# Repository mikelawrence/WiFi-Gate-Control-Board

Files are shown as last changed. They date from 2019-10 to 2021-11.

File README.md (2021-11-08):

# WiFi Gate Controller Board

This board performs the same functions as my [WiFi Gate Controller](https://github.com/mikelawrence/WiFi-Gate-Controller), which was designed to add WiFi and Home Assistant control to an existing US Automation Gate Opener board, while providing motor control and standard gate inputs. This board will replace a US Automation Gate Opener board. All inputs are now generalized and also support 10k resistor monitoring for safety devices like edge or photoelectric inputs.

This PCB design uses my custom libraries available here [Mike's KiCad Libraries](https://github.com/mikelawrence/KiCad-Libraries).

This PCB was designed with [KiCad 5.1.4](http://kicad.org).

_Note: Multiple ICs and Modules have exposed pads on the bottom which requires either a reflow oven or hot air to solder properly._

For Bill of Materials generation I use my version of [KiBoM](https://github.com/mikelawrence/KiBoM) forked from [SchrodingersGat](https://github.com/SchrodingersGat/KiBoM).

## Status

* Rev 1.1 PCB was built by and received from PCBWay.
  * This is a 4 layer PCB using 2 oz. copper for all layers and is relatively expensive.
  * Board has been assembled with no problems.
  * Motor interface still needs to be tested everything else is good.
  * You can order PCB from [PCBWay](https://www.pcbway.com/project/shareproject/WiFi_Gate_Control_Board_Rev_1_1.html).
  * You can order parts from Mouser using this [shared BOM](https://www.mouser.com/ProjectManager/ProjectDetail.aspx?AccessID=5c81251866).

* Rev 1.0 PCB was built by and received from PCBWay. Testing is complete.
  * PCBWay built the board.
  * I2C interface to TCA6424A, TCA6408A and LPC5024 verified. Reset not connected error found and corrected in Rev 1.1.
  * 12VDC input and reverse polarity protection verified.
  * LED circuitry and power supply verified.
  * All 12 Inputs verified. This includes switch closure and 10k monitoring.
  * All +12V switched outputs verified. Overload tested also.
  * All 2 Normally Open outputs tested.
  * Full-bridge motor control has been tested up to 30A. Far more than needed.
  * Motor current sensing verified. Removed U26 and connected IN input for each half-bridge directly to processor. Needed to set both half-bridges to active low so MIS offset could be measured unloaded.

## Board Preview

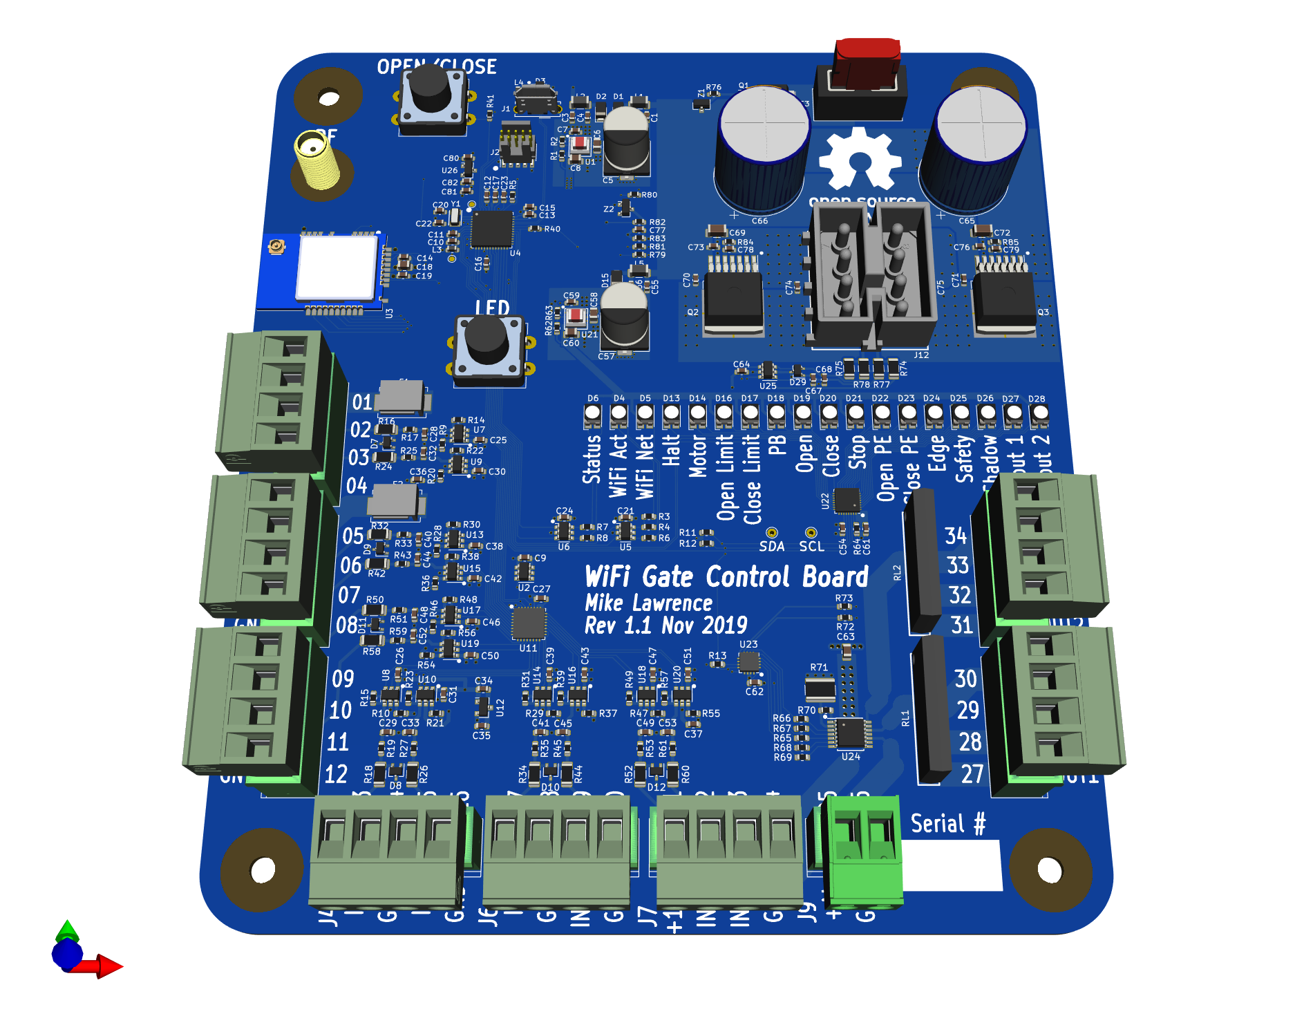
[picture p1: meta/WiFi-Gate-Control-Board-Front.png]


## Design

Intended to replace a US Automatic Patriot Board, this board can directly drive a single gate actuator in both directions. Multiple generic inputs are provided on board to make connection to existing standard gate functionality (open, close, pushbutton...) easy. By providing a WiFi connection to a MQTT server this board can be controlled via standard home automation software (Home Assistant).

Board size is 5.50" X 6.25". This board is smaller than the standard size of a US Automatic Patriot Board but matches existing spacer locations.

### Input Power

The main input connector (J12) provides connections to both the battery and motor. This connector is used by both US Automatic and Apollo gate openers. See pinout below.

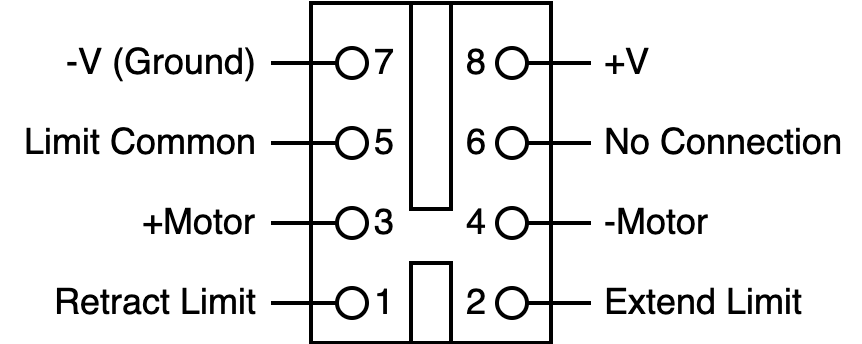
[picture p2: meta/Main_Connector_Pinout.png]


A 15 Amp fuse protects the entire board. DC input range is 12V nominal (5V - 17V). Idle input power consumption is pretty variable running from 69mW to 1.38W with an average around 179mW. Peak power is during WiFi transmit.

There are two identical power supplies. U1 powers most of the board via 3.3V. U1's power source is either main power (J12) or the USB connector (J1) so the microprocessor can be programmed on the bench without main power. All LEDs on the board are powered by a separate power supply (U21) which can be turned off by the microprocessor. This substantially reduces power consumption

### Board connections

There are nine screw terminal blocks with removable headers on the board used to connect with all gate functions.

| Terminal | Name  | Conn  | Description |
| :---: | :---: | :---: | :--- |
| 01 | +12V  | J3 | +12V power, Always on, fused 0.75A |
| 02 | IN1 | J3 | Input 1 (Radio) |
| 03 | IN2 | J3 | Input 2 |
| 04 | GND | J3 | Common Ground |
| 05 | +12V  | J5 | +12V power, Always on, fused 0.75A |
| 06 | IN3 | J5 | Input 3 |
| 07 | IN4 | J5 | Input 4 |
| 08 | GND | J5 | Common Ground |
| 09 | IN5 | J8 | Input 5 |
| 10 | GND | J8 | Common Ground |
| 11 | IN6 | J8 | Input 6 |
| 12 | GND | J8 | Common Ground |
| 13 | IN7 | J4 | Input 7 |
| 14 | GND | J4 | Common Ground |
| 15 | IN8 | J4 | Input 8 |
| 16 | GND | J4 | Common Ground |
| 17 | IN9 | J6 | Input 9 |
| 18 | GND | J6 | Common Ground |
| 19 | IN10  | J6 | Input 10 |
| 20 | GND | J6 | Common Ground |
| 21 | IN11  | J7 | +12V power, Switched PhotoEye power |
| 22 | GND | J7 | Input 11 |
| 23 | IN12  | J7 | Input 12 |
| 24 | GND | J7 | Common Ground |
| 25 | +AL | J9 | +12V power, Switched Alarm power |
| 26 | GND | J9 | Common Ground |
| 27 | OUT1  | J7 | Output 1, NO switch Output 1 |
| 28 | COM1  | J7 | Common 1, NO switch Output 1 |
| 29 | GND | J9 | Common Ground |
| 30 | +12V  | J9 | +12V power, Switched Output 1 power |
| 31 | OUT2  | J7 | Output 2, NO switch Output 2 |
| 32 | COM2  | J7 | Common 2, NO switch Output 2 |
| 33 | GND | J9 | Common Ground |
| 34 | +12V  | J9 | +12V power, Switched Output 2 power |

### Inputs

There are 12 identical physical inputs on this board. Each input can support Normally Open, Normally Closed, and 10k Monitored Normally Open inputs. A Normally Open input is a dry contact that is open when inactive and closed (shorted) when active. A Normally Closed input is the opposite; closed (shorted) when inactive and open when active. A 10k Monitored input is a Normally Open dry contact with a 8k to 10k resistor across the contacts and is normally used for safety inputs. The resistor allows the connections to the contact to be monitored while inactive. The most current efficient input is the Normally Open input which requires no additional current when inactive. The 10k Monitored input requires an additional 49μA and the Normally Closed input requires a 59μA per input while inactive.

Each input is actually a pair of connections: input and ground (negative terminal of battery). This means the ground side is the same (connected) on all inputs and external wiring must take this into account. Each input can be configured for different gate input types in software as shown in the table below.

| Input | Other Names | Type | Monitored | Action |
| :--- | :--- | :---: | :---: | :--- |
| Push Button | | NO | No | Cycle through Open/Stop/Close commands to gate. |
| Close | | NO | No | While active, close gate and holds it closed. |
| Open | Exit, Free Exit | NO | No | While active, opens gate and holds it open. |
| Stop | | NC | No | While active, stops the gate and holds it in position. |
| Open PhotoEye  | | NO or NC | Yes | While active, stops an opening gate or prevents gate from opening. |
| Close PhotoEye | | NO or NC | Yes | While active, reverses a closing gate to full open and holds it open. |
| Safety Edge | | NO | Yes | When activated, stops and momentarily reverses a moving gate. |
| Safety Loop | Reverse Loop | NO | Yes | While active, reverses a closing gate to full open and holds it open. |
| Shadow Loop | Center Loop, Under Gate Loop | NO | Yes | While active, prevents a closed gate from opening, prevents an open gate from closing, or reverses a closing gate to fully open and holds it open. |
| Input 1 | | NO or NC | Yes | Has no gate function. Can be used to monitor say a mailbox door.
| Input 2 | | NO or NC | Yes | Has no gate function.

Look at [Safety Edge Circuit calculations](drawings/Safety Edge Circuit calculations.pdf) for an explanation of how the input circuits with 10k monitoring work.

### Outputs

There are 4 switched power outputs on the board. J7 is used for PhotoEye connections and thus the +12V is switched on only during gate motion. The Alarm +AL is switched to +12V when alarm is active. The +12V on J10 and J11 output connectors are switched based on output settings.

There are several to be defined output settings here.

### SAMD ARM Processor and WiFi Module

The ARM processor and ATWINC1500 WiFi module are wired identical to the MKR1000 Arduino board, thus the Arduino development environment is used for software development and the ATWINC1500 module is directly supported.

## Setup

### Arduino Setup

This board is designed to mimic a [MKR1000](https://store.arduino.cc/usa/arduino-mkr1000) board from Arduino. Make sure the the MKR1000 board is supported by installing. Do this by opening the Board Manager as shown below.

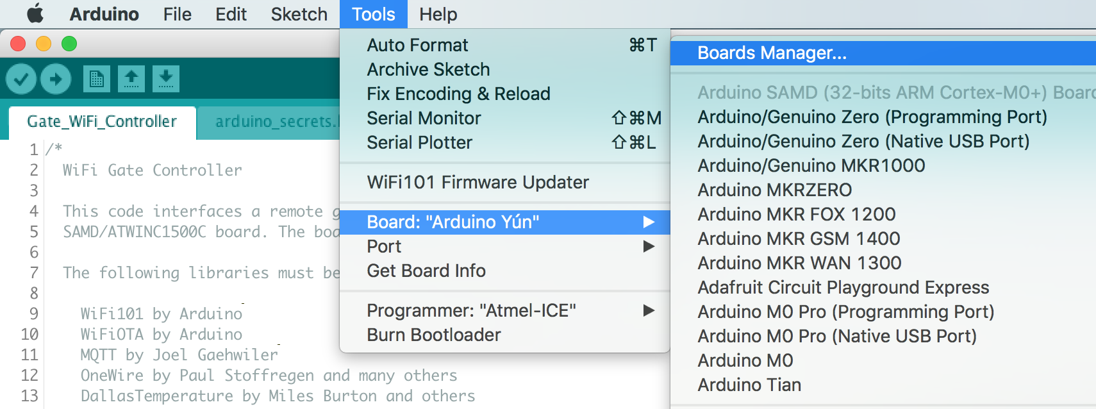
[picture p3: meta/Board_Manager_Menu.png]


Type in "samd" in the filter edit and you will see several options. Select "Arduino SAMD Boards (32-bits ARM Cortex-M0+)" and install the latest version as shown below.

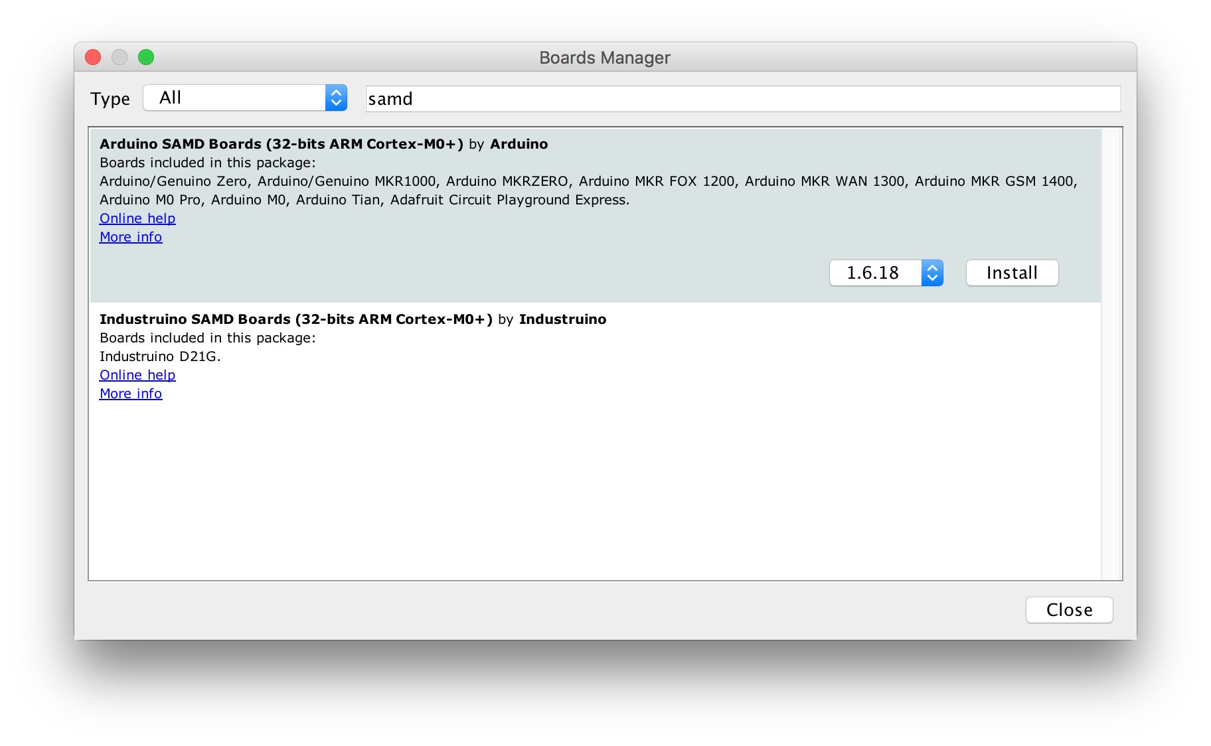
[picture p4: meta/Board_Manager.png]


It will take a few minutes to download and install the board package. Once complete it's time to install the necessary libraries. Start by opening the Library Manager as shown below.

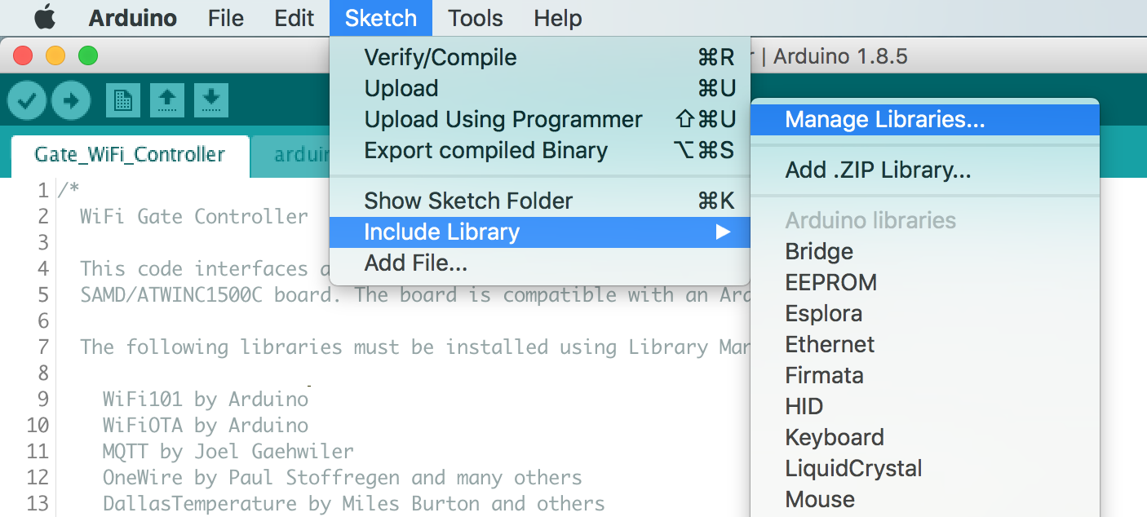
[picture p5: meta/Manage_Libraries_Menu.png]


Type in "mqtt" in the filter edit and scroll down until you see "MQTT by Joel Gaehwiler" as shown below.

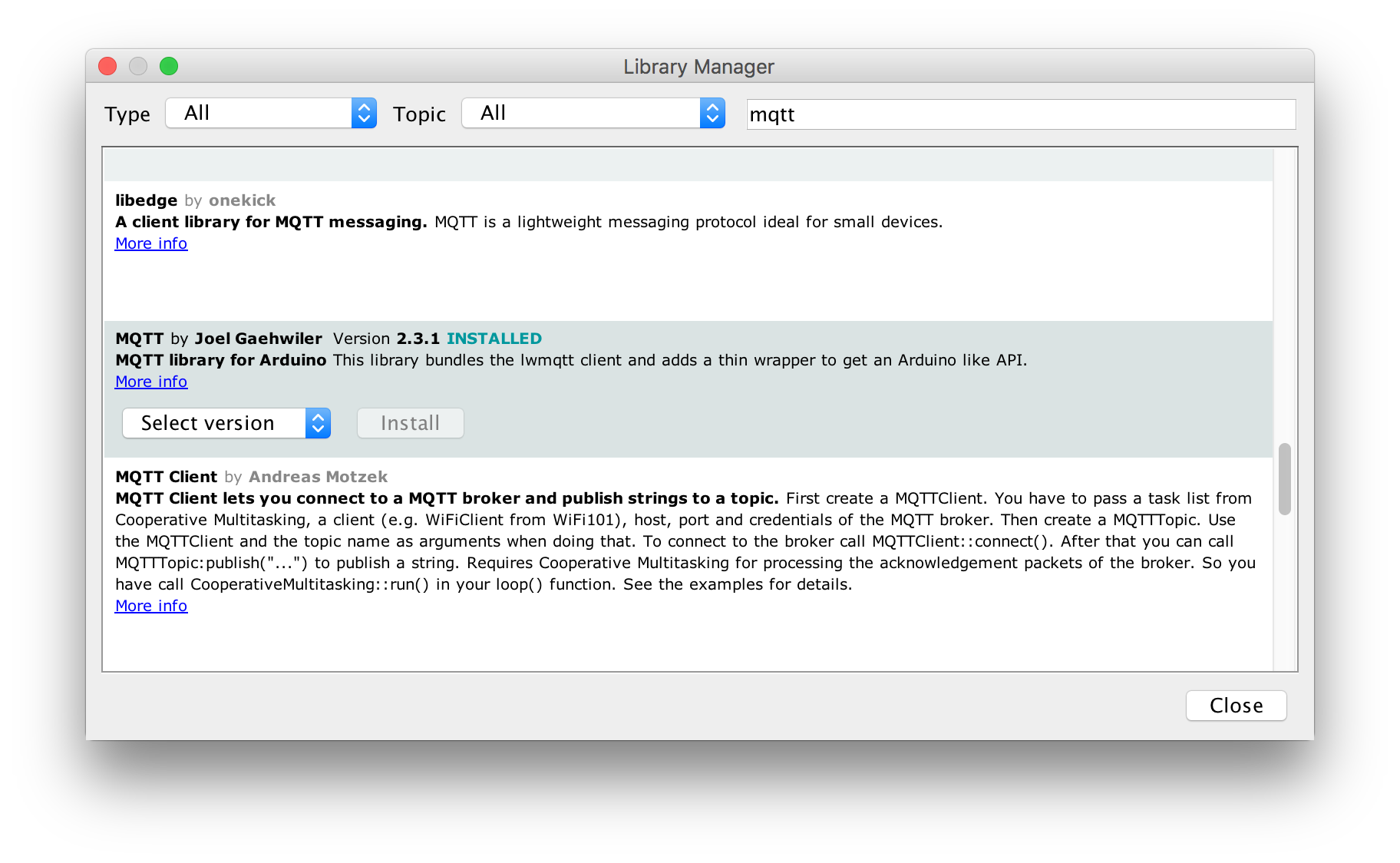
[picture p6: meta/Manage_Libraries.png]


Once "MQTT" is installed repeat the install for the following libraries.

* WiFi101 by Arduino
* WiFi101OTA by Arduino
* SD by Arduino
* FreeRTOS_SAMD21 by BriscoeTech
* I2C_DMAC version by Martin Lindupp

### Board Setup

The Arduino development environment expects a bootloader in the SAMD ARM processor which will allow programming via USB. The bootloader must be programmed first using a supported programming pod. I used an "Atmel-ICE" pod but there are other options. First make sure you have selected the "Arduino/Genuino MKR1000" board as shown below.

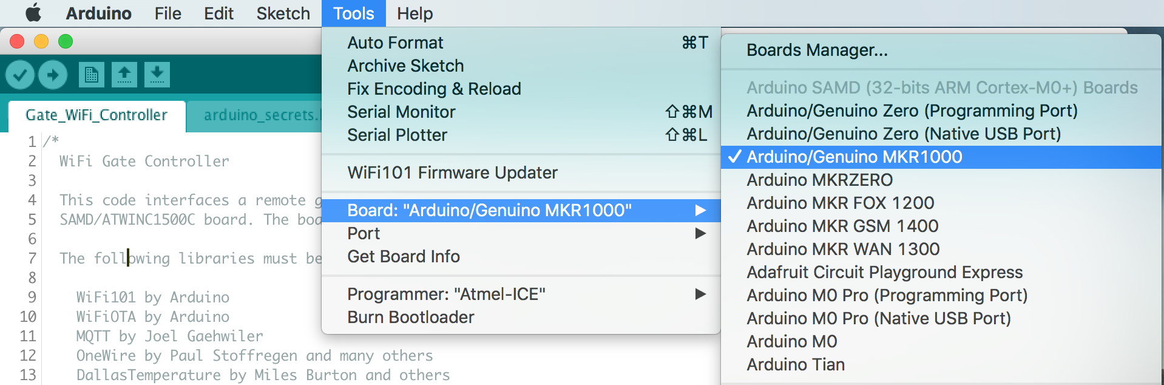
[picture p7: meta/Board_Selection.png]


Next select your programmer.

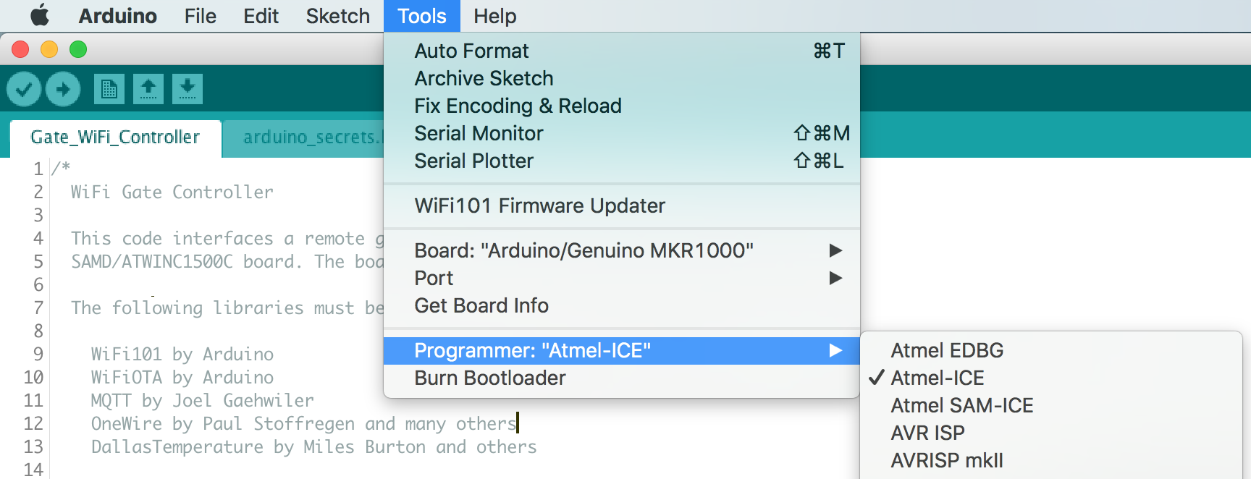
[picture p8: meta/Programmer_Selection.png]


Make sure the board is powered via USB and the programmer is connected to the debug connector then select "Burn Bootloader".

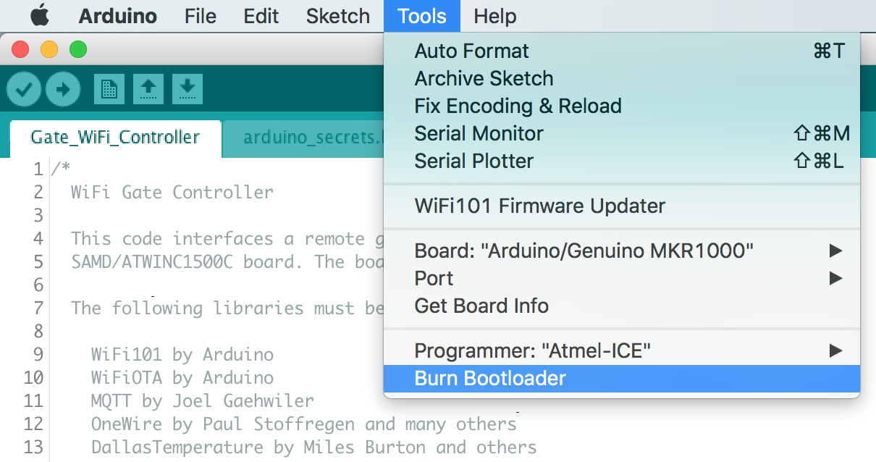
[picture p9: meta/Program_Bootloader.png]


Now the bootloader is programmed it's time to load the "WiFi101 FirmwareUpdater" example. This will update the firmware in the ATWINC1500 module.

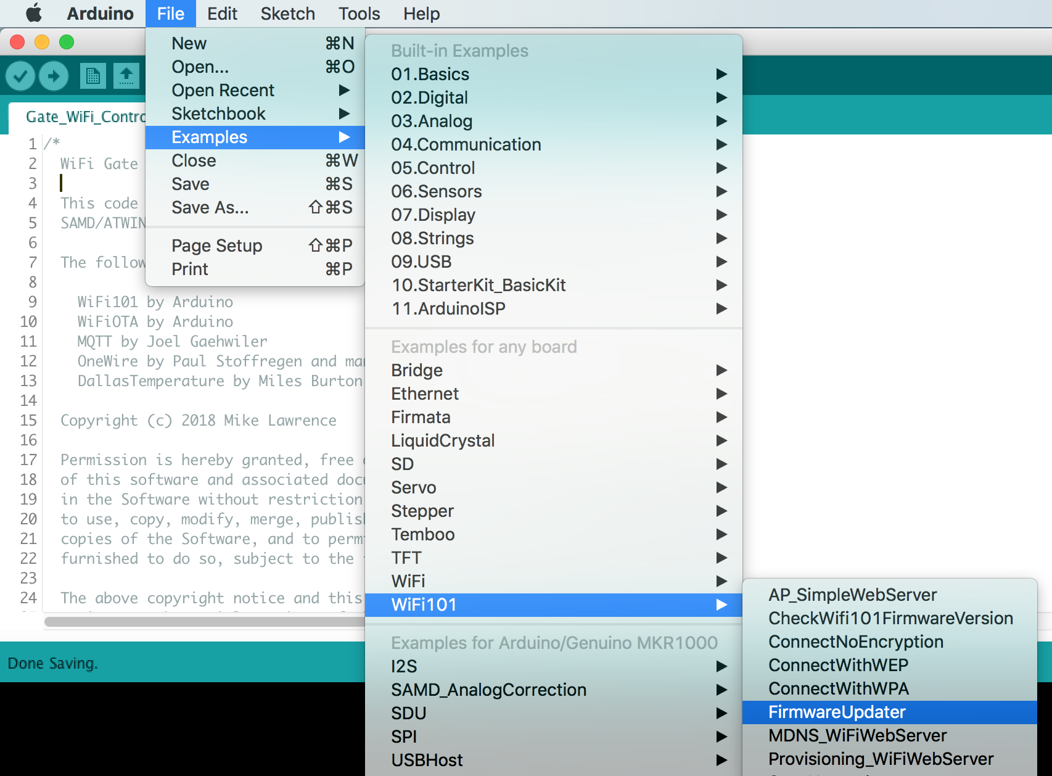
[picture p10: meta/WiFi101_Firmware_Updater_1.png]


Now "Upload" the "WiFi101 FirmwareUpdater" example.

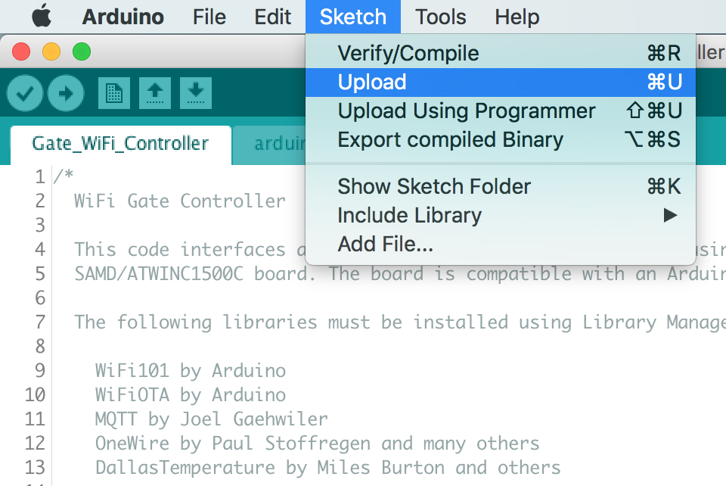
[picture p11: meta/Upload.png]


Update the ATWINC1500 module by selecting "WiFi101 Firmware Updater".

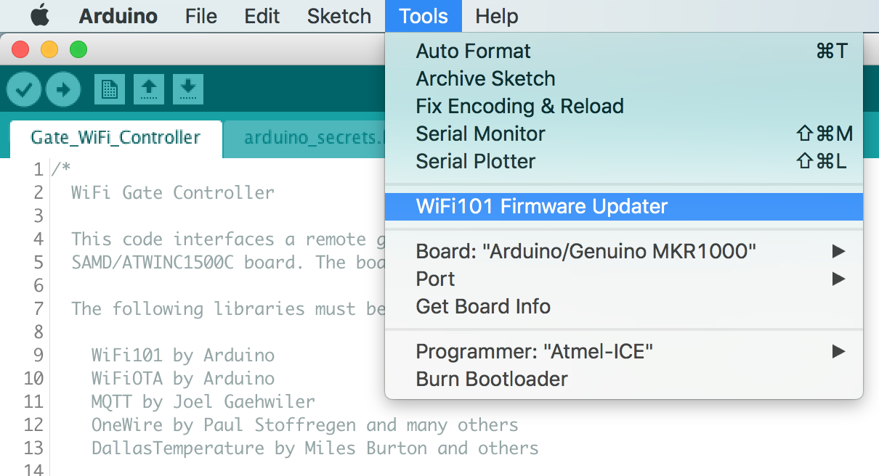
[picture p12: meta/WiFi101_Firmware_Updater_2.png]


Select the latest WINC1501 Model B firmware and click the "Update Firmware" button.

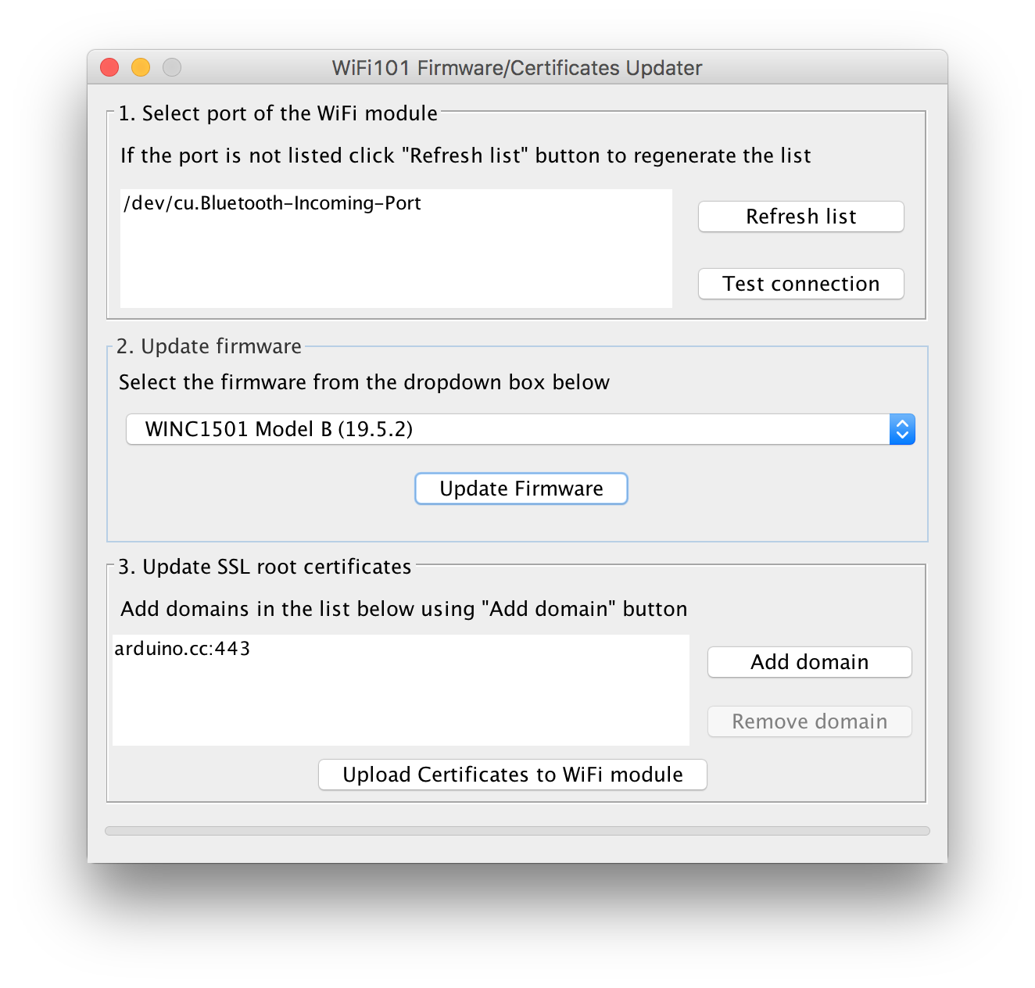
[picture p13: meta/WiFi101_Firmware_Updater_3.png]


Finally open the "WiFi_Gate_Controller.ino" sketch downloaded from GitHub. Update the necessary defines for your Wireless network and MQTT server settings see the [Code README](code/README.md) for more information. Now upload it just like the "WiFi101 FirmwareUpdater" example. All done!

This project also supports Visual Studio Code. Visual Studio Code supports building Arduino projects and IntelliSense with code completion. The included settings files support my MacOS environment. Just do a search for "Visual Studio Code Arduino" to see how to install.

## Acknowledgments

* [Arduino](www.arduino.cc) kindly develops open source hardware and software which makes writing software for this board and especially the WiFi module easy.
* [Visual Studio Code](https://code.visualstudio.com/) from Microsoft is a great alternative to the Arduino IDE.

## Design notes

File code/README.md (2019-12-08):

# WiFi Gate Control Board Sketch
The WiFi Gate Control Board Sketch is written in C++. It replaces the functionality of a US Automatic Gate Control Board while adding IOT and Automation via WiFi. The sketch is a discoverable cover and sensor for [Home Assistant](https://home-assistant.io/), an open-source home automation platform running on Python. [MQTT](http://mqtt.org/), a machine-to-machine (M2M)/"Internet of Things" connectivity protocol, is the basis of communication with Home Assistant.

## Status
This software is in the development stage.
* Uses FreeRTOS to prevent Arduino's WiFi101 library from blocking gate functionality when there are network problems.
* Network is fully functional including MQTT connectivity.
* Hardware Access Layer (HAL) supports the 12 board inputs including mapping to gate inputs.
* Error module supports hard faults which stop the board from doing anything and general errors with Status LED indication.
* Basic Home Assistant automatic configuration via MQTT is in place but does nothing yet.

# Setup
## Sketch Setup
Build defines in [WiFi_Gate_Control_Board.h](WiFi_Gate_Control_Board/WiFi_Gate_Control_Board.h) control how the sketch is built.

```c
/******************************************************************
 * Build defines
 ******************************************************************/
// Enable Watchdog Timer
#define ENABLE_WATCHDOG
// Enable OTA updates
#define ENABLE_OTA_UPDATES
// Enable Serial on USB
#define ENABLE_SERIAL
// Enable Low Power Mode on WiFi
#define ENABLE_WIFI_LOW_POWER
// enable calibration mode
#define ENABLE_CALIBRATION_MODE
// Current Version
#define VERSION                   "1.0"

/******************************************************************
 * Application defines
 ******************************************************************/
// Name of this board, each board should be unique
// Used as MQTT Client ID, HASS Name, and OTA Name
#define BOARD_NAME                "New Front Gate"
// input debounce time in milliseconds
#define DEBOUNCE_TIME             100
// temperature measurement time in milliseconds, Must be greater than 5 seconds
#define TEMP_RATE                 (1*60*1000)
// Length of time in milliseconds LEDS stay on after pushbutton input
#define LED_ON_TIME               (5*60*1000)
// NTP server used to update local time, can be IP Address or name
#define NTP_SERVER                "pool.ntp.org"
//#define NTP_SERVER                "time.nist.gov"
// timezone difference from GMT in hours (Standard Time difference)
#define TZDIFF                    -6

/******************************************************************
 * Gate Defines
 *   Here is where you change the basic gate settings
 ******************************************************************/
// this defines which way the linear actuator has to move to open
//   GATE_PULL_TO_OPEN or GATE_PUSH_TO_OPEN
#define GATE_DIRECTION            GATE_PULL_TO_OPEN

/******************************************************************
 * Gate Input Type Defines
 *   Here is where you change the board inputs to specific types
 *   Look in hal.h for IN_Type_Enum for valid input types
 ******************************************************************/
#define BOARD_IN1                 IN_TYPE_PUSHBUTTON_NO
#define BOARD_IN2                 IN_TYPE_NONE
#define BOARD_IN3                 IN_TYPE_NONE
#define BOARD_IN4                 IN_TYPE_NONE
#define BOARD_IN5                 IN_TYPE_PUSHBUTTON_NO
#define BOARD_IN6                 IN_TYPE_OPEN_NO
#define BOARD_IN7                 IN_TYPE_NONE
#define BOARD_IN8                 IN_TYPE_NONE
#define BOARD_IN9                 IN_TYPE_NONE
#define BOARD_IN10                IN_TYPE_NONE
#define BOARD_IN11                IN_TYPE_OPEN_PHOTOEYE_10K
#define BOARD_IN12                IN_TYPE_NONE

/******************************************************************
 * Gate Output Type Defines
 *   Here is where you change the board outputs to specific types
 ******************************************************************/

/******************************************************************
 * Home Assistant MQTT Defines
 ******************************************************************/
#define HASS_PREFIX               "homeassistant"
#define HASS_GATE_NAME            "new_front_gate"    // should be BOARD_NAME with no whitespace
```

* When "ENABLE_WATCHDOG" is defined the Watchdog Timer is enabled with a 16 second timeout. This will reset the ARM processor is something goes wrong.
* When "ENABLE_OTA_UPDATES" is defined the sketch can be updated using Arduino's Over-The-Air Update capability.
* When "ENABLE_SERIAL" is defined then status information is sent out the serial connection which in this case is the USB port. Otherwise the serial port won't even be enabled.
* When "ENABLE_WIFI_LOW_POWER" is defined the WINC1500 module is set to Low Power Mode. This can drop the current requirements of the module to a third or even less. Low Power Mode reduces the transmit frequency to the beacon interval and may also cause the module to hang occasionally.
* When "ENABLE_CALIBRATION_MODE" is defined the sketch is put into calibration mode. This is an allows the user to calibrate the Motor Current Sense ADC input at 15 amps and 25 C.
* "BOARD_NAME" names the board so multiple instances of this board can on the WiFi network at the same time. It is used is several places including Home Assistant Name, OTA Name, and MQTT Client ID. This is a string.
* "DEBOUNCE_TIME" is how long to ignore contact changes on the input before accepting them as valid. This is an integer and the units are milliseconds.
* "TEMP_RATE" is how often the temperature should be sampled and updated via MQTT.  This is an integer and the units are milliseconds. The time must be greater than 5000 milliseconds.
* "NTP_SERVER" is name of the NTP server used to synchronize time. This can be a DNS name like "pool.ntp.org" or an IP address 192.168.1.123.
* "TZDIFF" is the UTC to actual time zone difference in hours.
* "LED_ON_TIME" is how long the LED's on the board will stay on after the LED button is pushed.
* 'GATE_DIRECTION' is a define used to set the direction of the gate. Either "GATE_PULL_TO_OPEN" or "GATE_PUSH_TO_OPEN".
* 'BOARD_IN1-BOARD_IN12' defines the type of input for each of the generic inputs on the board.
  * IN_TYPE_NONE means the input is not active.
  * IN_TYPE_OPEN_LIMIT_NO means normally open switch Open Limit input.
  * IN_TYPE_CLOSE_LIMIT_NO means normally open switch Close Limit input.
  * IN_TYPE_PUSHBUTTON_NO means normally open switch Open/Stop/Close input (pushbutton toggle).
  * IN_TYPE_PUSHBUTTON_NC means normally closed switch Open/Stop/Close input (pushbutton toggle).
  * IN_TYPE_OPEN_NO means normally open switch Open input.
  * IN_TYPE_OPEN_NC means normally closed switch Open input.
  * IN_TYPE_CLOSE_NO means normally open switch Close input.
  * IN_TYPE_CLOSE_NC means normally closed switch Close input.
  * IN_TYPE_STOP_NO means normally open switch Stop input.
  * IN_TYPE_STOP_NC means normally closed switch Stop input.
  * IN_TYPE_OPEN_PHOTOEYE_NO means normally open PhotoEye open input.
  * IN_TYPE_OPEN_PHOTOEYE_NC means normally closed PhotoEye open input.
  * IN_TYPE_OPEN_PHOTOEYE_10K means normally open PhotoEye open input with 10k monitoring.
  * IN_TYPE_CLOSE_PHOTOEYE_NO means normally open PhotoEye close input.
  * IN_TYPE_CLOSE_PHOTOEYE_NC means normally closed PhotoEye close input.
  * IN_TYPE_CLOSE_PHOTOEYE_10K means normally open PhotoEye close input with 10k monitoring.
  * IN_TYPE_EDGE_NO means normally open Edge input.
  * IN_TYPE_EDGE_NC means normally closed Edge input.
  * IN_TYPE_EDGE_10K means normally open Edge input with 10k monitoring.
  * IN_TYPE_SAFETY_NO means normally open Safety input.
  * IN_TYPE_SAFETY_NC means normally closed Safety input.
  * IN_TYPE_SAFETY_10K means normally open Safety input with 10k monitoring.
  * IN_TYPE_SHADOW_NO means normally open Shadow input.
  * IN_TYPE_SHADOW_NC means normally closed Shadow input.
  * IN_TYPE_SHADOW_10K means normally open Shadow input with 10k monitoring.
  * IN_TYPE_INPUT1_NO means normally open Input 1 input.
  * IN_TYPE_INPUT1_NC means normally closed Input 1 input.
  * IN_TYPE_INPUT1_10K means normally open Input 1 input with 10k monitoring.
  * IN_TYPE_INPUT2_NO means normally open Input 2 input.
  * IN_TYPE_INPUT2_NC means normally closed Input 2 input.
  * IN_TYPE_INPUT2_10K means normally open Input 2 input with 10k monitoring.
* "HASS_PREFIX" is the Home Assistant MQTT Discovery Prefix as defined in your system. This is a string.
* "HASS_GATE_NAME" is used in the MQTT topics to identify the cover and sensor to Home Assistant. Home Assistant calls this the node id. It is a string and must not contain special characters including a space.

The arduino_secrets.h file is not included on Github. You must create and edit it to meet your configuration.

```c
/******************************************************************
 * arduino_secrets.h
 ******************************************************************/
 /******************************************************************
  * WiFI Setup
  ******************************************************************/
 #define SECRET_SSID             "SSID of your WiFi network"
 #define SECRET_PASSWORD         "Password for your WIFi network"

 /******************************************************************
  * MQTT Setup
  ******************************************************************/
 #define MQTT_SERVER             "mqtt.local"
 #define MQTT_SERVERPORT         1883
 #define MQTT_USERNAME           "MQTT username"
 #define MQTT_PASSWORD           "MQTT password"

 /******************************************************************
  * OTA Setup
  ******************************************************************/
 #define OTA_PASSWORD            "OTA password"
```

## Home Assistant Setup
ToDo.

## Calibration
ToDo.

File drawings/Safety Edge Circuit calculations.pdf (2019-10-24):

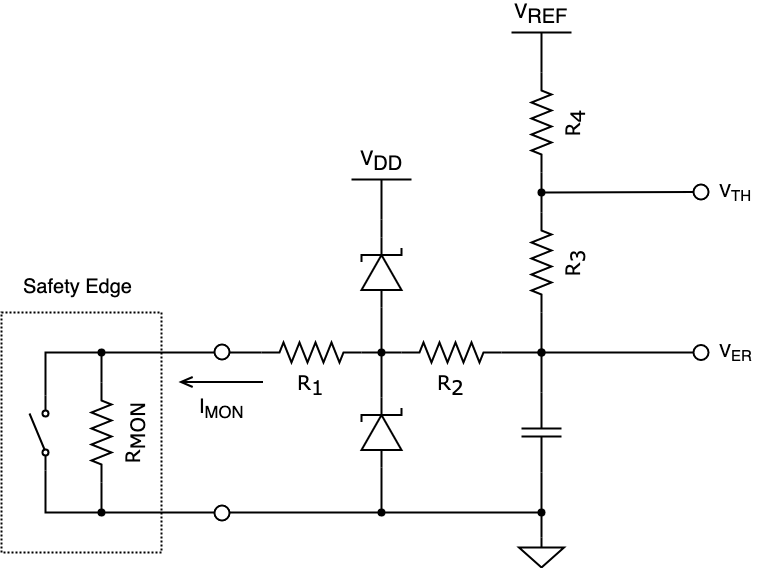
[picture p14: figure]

VREF (V) | 2.5 | | VTH for R4 calc (V) | 1.250
R1 (Ω) | 1000 | Std 1% | R4 calc (Ω) | 24759
R2 (Ω) | 10000 | Std 1% | VTH Short (V) | 1.018
R3 (Ω) | 6040 | Std 1% | VTH Min (V) | 1.246
R4 (Ω) | 24900 | Std 1% | VTH 8K (V) | 1.257
RMON Short (Ω) | 50 | | VTH 10K (V) | 1.302
RMON Min (Ω) | 7719 | | VTH Max (V) | 1.313
RMON 8K (Ω) | 8125 | | IMON Max (µA) | 50
RMON 10K (Ω) | 10000 | | VER Max (V) | 1.025
RMON Max (Ω) | 10500

Safety Edge Circuit

Eq1

Eq2

From Eq1

## VTH = RMON + R1 + R2 + R3 RMON + R1 + R2 + R3 + R4

VREF

VER = RMON + R1 + R2

## RMON + R1 + R2 + R3 + R4

VREF

R4 = (
| VREF
VTH

− 1

## ) (RMON + R1 + R2 + R3)

1

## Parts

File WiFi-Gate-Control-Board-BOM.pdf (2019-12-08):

Quantity | References | Value | Description | Manufacturer | Part Number | Vendor | Vendor Part Number
6 | C1 C2 C3 C4 C55 C56 | 1nF | CAP, 0603, 1nF, 10%, X7R, 10V | Vishay | VJ0603Y102KXAAC31 | Mouser | 77-VJ0603Y102KXAAC31
2 | C5 C57 | 100uF | CAP, SMD 8X10, 100uF, 20%, EC, 35V | United Chemi-Con | EMVH350ADA101MHA0G | Mouser | 661-EMVH350ADA101M
6 | C6 C8 C18 C58 C60 C63 | 22uF | CAP, 0805, 22uf, 20%, X5R, 25V | Taiyo Yuden | TMK212BBJ226MG-TT | Mouser | 963-TMK212BBJ226MGTT
2 | C7 C59 | 3.3nF | CAP, 0603, 3.3nF, 5%, X7R, 10V | Vishay | VJ0603Y332JXQPW1BC | Mouser | 77-VJ0603Y332JXQPBC
33 | C9 C11 C12 C13 C14 C16 C21 C23 C24 C25 C26 C27 C30 C31 C34 C36 C37 C38 C39 C42 C43 C46 C47 C50 C51 C62 C64 C73 C76 C78 C79 C80 C82 | 0.1uF | CAP, 0603, 0.1uF, 5%, X7R, 50V | Yageo | CC603JRX7R9BB104 | Mouser | 603-CC603JRX7R9BB104
3 | C10 C15 C81 | 4.7uF | CAP, 0603, 4.7uf, 10%, X7R, 6.3V | Taiyo Yuden | JMK107BB7475KA-T | Mouser | 963-JMK107BB7475KA-T
17 | C17 C19 C28 C29 C32 C33 C35 C40 C41 C44 C45 C48 C49 C52 C53 C54 C61 | 1uF | CAP, 0603, 1uF, 10%, X5R, 50V | Taiyo Yuden | UMK107BJ105KA-T | Mouser | 963-UMK107BJ105KA-T
2 | C20 C22 | 15pF | CAP, 0603, 15pF, 5%, C0G, 50V | AVX | 06035A150JAT2A | Mouser | 581-06035A150J
2 | C65 C66 | 470uF | CAP, THT 16X15, 470uF, 20%, EC, 35V | Nichicon | UPM1V471MHD6 | Mouser | 647-UPM1V471MHD6
2 | C67 C68 | DNI | CAP, 0603, Not Installed
2 | C69 C72 | 10uF | CAP, 1206, 10uF, 10%, X7R, 50V | TDK | CGA5L1X7R1H106K160AC | Mouser | 810-CGA5L1X7R1H106K1
4 | C70 C71 C74 C75 | 0.22uF | CAP, 0603, 0.22uF, 10%, X7R, 50V | Taiyo Yuden | UMK107B7224KA-TR | Mouser | 963-UMK107B7224KA-TR
1 | C77 | 10nF | CAP, 0603, 10nF, 5%, X7R, 50V | Vishay | VJ0603Y103JXACW1BC | Mouser | 77-VJ0603Y103JXACBC
3 | D1 D2 D15 | DFLS130 | DIO, PowerDI123, Schottky Rectifier, 30V, 1A | Diodes Inc | DFLS130LQ | Mouser | 621-DFLS130L
1 | D3 | PRTR5V0U2X | TVS, SOT143, ESD Protection, USB | Nexperia | PRTR5V0U2X,215 | Mouser | 771-PRTR5V0U2X-T/R
18 | D4 D5 D6 D13 D14 D16 D17 D18 D19 D20 D21 D22 D23 D24 D25 D26 D27 D28 | Red/Green | LED, PLCC4, Red/Green | Avago | HSMF-A203-A00J1 | Mouser | 630-HSMF-A203-A00J1
7 | D7 D8 D9 D10 D11 D12 D29 | TPD2E2U06 | TVS, SC70-3, ESD TVS Protection, Dual | Texas Instruments | TPD2E2U06QDCKRQ1 | Mouser | 595-TPD2E2U06QDCKRQ1
2 | F1 F2 | 0.75A | Fuse, PTC Resettable, 0.75A, SMT | Bourns | MFSM075-2 | Mouser | 652-MFSM075-2
1 | F3 | 15A | Fuse, Mini Fuse Holder | Keystone | 3568 | Mouser | 534-3568
1 | J1 | USB_B_Micro | CON, THT, Micro USB 2.0 Type AB, Vertical | Wurth Electronics | 614105150721 | Mouser | 710-614105150621
1 | J2 | Cortex Debug | CON, SMD, 1.27mm Header, Dual Row, Vertical, 10 Pos | Samtec | FTSH-105-01-L-DV-K | Mouser | 200-FTSH10501LDVK
8 | J3 J4 J5 J6 J7 J8 J10 J11 | Screw Header 4 Pos | CON, THT, 5.08mm Pluggable Terminal Header, 4 Pos | Phoenix Contact | 1755752 | Mouser | 651-1755752
8 | | Screw Header 4 Pos | CON, THT, 5.08mm Pluggable Terminal Plug, 4 Pos | Phoenix Contact | 1757035 | Mouser | 651-1757035
1 | J9 | Screw Header 2 Pos | CON, THT, 5.08mm Pluggable Terminal Header, 2 Pos | Phoenix Contact | 1755736 | Mouser | 651-1755736
1 | | Screw Header 2 Pos | CON, THT, 5.08mm Pluggable Terminal Plug, 2 Pos | Phoenix Contact | 1757019 | Mouser | 651-1757019
1 | J12 | Motor | CON, THT, MATE-N-LOK, Dual Row, 8 Pos | TE Connectivity | 350212-1 | Mouser | 571-3502121

# WiFi Gate Control Board BOM Rev 1.1

Quantity | References | Value | Description | Manufacturer | Part Number | Vendor | Vendor Part Number
3 | L1 L2 L5 | 1k@100MHz | BEAD, 1206, 1k@100MHz, 2A | Murata | BLM31KN102SH1L | Mouser | 81-BLM31KN102SH1L
2 | L3 L4 | 470@100MHz | BEAD, 0603, 470R@100MHz, 1A | Murata | BLM18PG471SN1D | Mouser | 81-BLM18PG471SN1D
1 | Q1 | IPD90P03P4L-04 | TRANSISTOR, TO-252-3, P-CH, -90A, -30V | Infineon | IPD90P03P4L-04 | Mouser | 726-IPD90P03P4L04
2 | Q2 Q3 | IFX007T | IC, Motor Driver, Half Bridge, 55A | Infineon | IFX007TAUMA1 | Mouser | 726-IFX007TAUMA1
2 | R1 R62 | 1.21M | RES, 0603, 1.21M, 1/10W, 1%, T100 | Yageo | RC0603FR-071M21L | Mouser | 603-RC0603FR-071M21L
2 | R2 R63 | 383k | RES, 0603, 383k, 1/10W, 1%, T100 | Panasonic | ERJ-3EKF3833V | Mouser | 667-ERJ-3EKF3833V
5 | R3 R4 R6 R7 R8 | 44.2R | RES, 0603, 44.2R, 1/10W, 1%, T100 | Panasonic | ERJ-3EKF44R2V | Mouser | 667-ERJ-3EKF44R2V
1 | R5 | 39R | RES, 0603, 39R, 1/10W, 1%, T100 | Panasonic | ERJ-3EKF39R0V | Mouser | 667-ERJ-3EKF39R0V
12 | R9 R10 R20 R21 R28 R29 R36 R37 R46 R47 R54 R55 | 33.2k | RES, 0603, 33.2k, 1/16W, 0.5%, T25 | Susumu | RR0816P-3322D51C | Mouser | 754-RR0816P-3322D51C
3 | R11 R12 R13 | 4.7k | RES, 0603, 4.7k, 1/10W, 1%, T100 | Panasonic | ERJ-3EKF4701V | Mouser | 667-ERJ-3EKF4701V
12 | R14 R15 R22 R23 R30 R31 R38 R39 R48 R49 R56 R57 | 6.81k | RES, 0603, 6.81k, 1/16W, 0.5%, T25 | Susumu | RR0816P-6811D81H | Mouser | 754-RR0816P-6811D81H
14 | R16 R18 R24 R26 R32 R34 R42 R44 R50 R52 R58 R60 R77 R78 | 1k | RES, 1206, 1k, 1/4W, 0.5%, T100 | Yageo | AC1206DR-071KL | Mouser | AC1206DR-071KL
22 | R17 R19 R25 R27 R33 R35 R43 R45 R51 R53 R59 R61 R66 R67 R68 R69 R76 R79 R80 R81 R84 R85 | 10k | RES, 0603, 10k, 1/16W, 0.5%, T25 | Susumu | RR0816P-103-D | Mouser | 754-RR0816P-103D
3 | R40 R41 R65 | 100k | RES, 0603, 100k, 1/10W, 1%, T100 | Panasonic | ERJ-3EKF1003V | Mouser | 667-ERJ-3EKF1003V
1 | R64 | 2.94k | RES, 0603, 2.94k, 1/10W, 1%, T100 | Panasonic | ERJ-3EKF2941V | Mouser | 667-ERJ-3EKF2941V
1 | R70 | 2.2k | RES, 0603, 2.2k, 1/10W, 1%, T100 | Panasonic | ERJ-3EKF2201V | Mouser | 667-ERJ-3EKF2201V
1 | R71 | 150R | RES, 1218, 150R, 1W, 1%, T100 | Vishay / Dale | CRCW1218150RFKEK | Mouser | 71-CRCW1218-150-E3
2 | R72 R73 | 422R | RES, 0603, 422R, 1/10W, 1%, T100 | Panasonic | ERJ-3EKF4220V | Mouser | 667-ERJ-3EKF4220V
2 | R74 R75 | 330k | RES, 1206, 330k, 2/3W, 5%, T200 | Panasonic | ERJ-P08J334V | Mouser | 667-ERJ-P08J334V
2 | R82 R83 | 1k | RES, 0603, 1k, 1/10W, 1%, T100 | Panasonic | ERJ-3EKF1001V | Mouser | 667-ERJ-3EKF1001V
2 | RL1 RL2 | CPC1511Y | MODULE, THT, SSR, Normally Open, 450mA | IXYS | CPC1511Y | Mouser | 849-CPC1511Y
2 | SW1 SW2 | ~ | SW, THT, Push Button | Wurth Electronics | 430476085716 | Mouser | 710-430476085716
2 | U1 U21 | LMZ21700 | MODULE, SMD, Simple Switcher, 17V, 650mA | Texas Instruments | LMZ21700SILR | Mouser | 595-LMZ21700SILR
1 | U2 | TMP100 | IC, SOT-23-6, I2C Temperature Sensor | Texas Instruments | TMP100AQDBVRQ1 | Mouser | 595-TMP100AQDBVRQ1
1 | U3 | ATWINC1500-MR210UB | MODULE, SMD, WiFi, u.FL connector | Microchip | ATWINC1500-MR210UB1140 | Mouser | 579-C1500MR210UB1140
1 | U4 | SAMD21G18-M | IC, QFN44, MCU, ARM, 256kB Flash, 32kB SRAM, 48MHz | Microchip | ATSAMD21G18A-MUT | Mouser | 556-ATSAMD21G18A-MUT
1 | U5 | 74LVC2G07 | IC, SOT-23-6, Dual Buffer with Open-Drain Outputs | Texas Instruments | SN74LVC2G07DBVR | Mouser | 595-SN74LVC2G07DBVR
1 | U6 | 74LVC2G06 | IC, SOT-23-6, Dual Inverter with Open-Drain Outputs | Texas Instruments | SN74LVC2G06DBVR | Mouser | 595-SN74LVC2G06DBVR

Quantity | References | Value | Description | Manufacturer | Part Number | Vendor | Vendor Part Number
12 | U7 U8 U9 U10 U13 U14 U15 U16 U17 U18 U19 U20 | TPS3779 | IC, SOT-23-6, Dual Voltage Detector | Texas Instruments | TPS3779BDBVR | Mouser | 595-TPS3779BDBVR
1 | U11 | TCA6424A | IC, QFN-32, I2C IO Expander | Texas Instruments | TCA6424ARGJR | Mouser | 595-TCA6424ARGJR
1 | U12 | REF3330 | IC, SOT-23, Voltage Reference, 3.0V, 30ppm | Texas Instruments | REF3330AIDBZR | Mouser | 595-REF3330AIDBZR
1 | U22 | LP5024 | IC, QFN-32, 24-Channel, I2C LED Driver | Texas Instruments | LP5024RSMR | Mouser | 595-LP5024RSMR
1 | U23 | TCA6408A | IC, VQFN-16, I2C IO Expander | Texas Instruments | TCA6408ARGTR | Mouser | 595-TCA6408ARGTR
1 | U24 | ITS4075Q | IC, PG-TSDSO-14, 4-Channel, High-Side Power Switch | Infineon | ITS4075Q-EP-DXUMA1 | Mouser | 726-ITS4075QEPDXUMA1
1 | U25 | 74LVC2G17 | IC, SOT-23-6, Dual Schmitt-Trigger Buffer | Texas Instruments | SN74LVC2G17DBVR | Mouser | 595-SN74LVC2G17DBVR
1 | U26 | REF3325 | IC, SOT-23, Voltage Reference, 2.5V, 30ppm | Texas Instruments | REF3325AIDBZR | Mouser | 595-REF3325AIDBZR
1 | Y1 | 32.768kHz | XTL, SMD, 32.768kHz | Abracon | ABS07-32.768KHZ-9-T | Mouser | 815-ABS07-32.768K9T
1 | Z1 | 10V | Zener, 10V, SOT-23 | On Semiconductor | SZBZX84C10LT1G | Mouser | 863-SZBZX84C10LT1G
1 | Z2 | 2.7V | Zener, 2.5V, SOT-23 | On Semiconductor | SZBZX84C2V7LT1G | Mouser | 863-SZBZX84C2V7LT1G

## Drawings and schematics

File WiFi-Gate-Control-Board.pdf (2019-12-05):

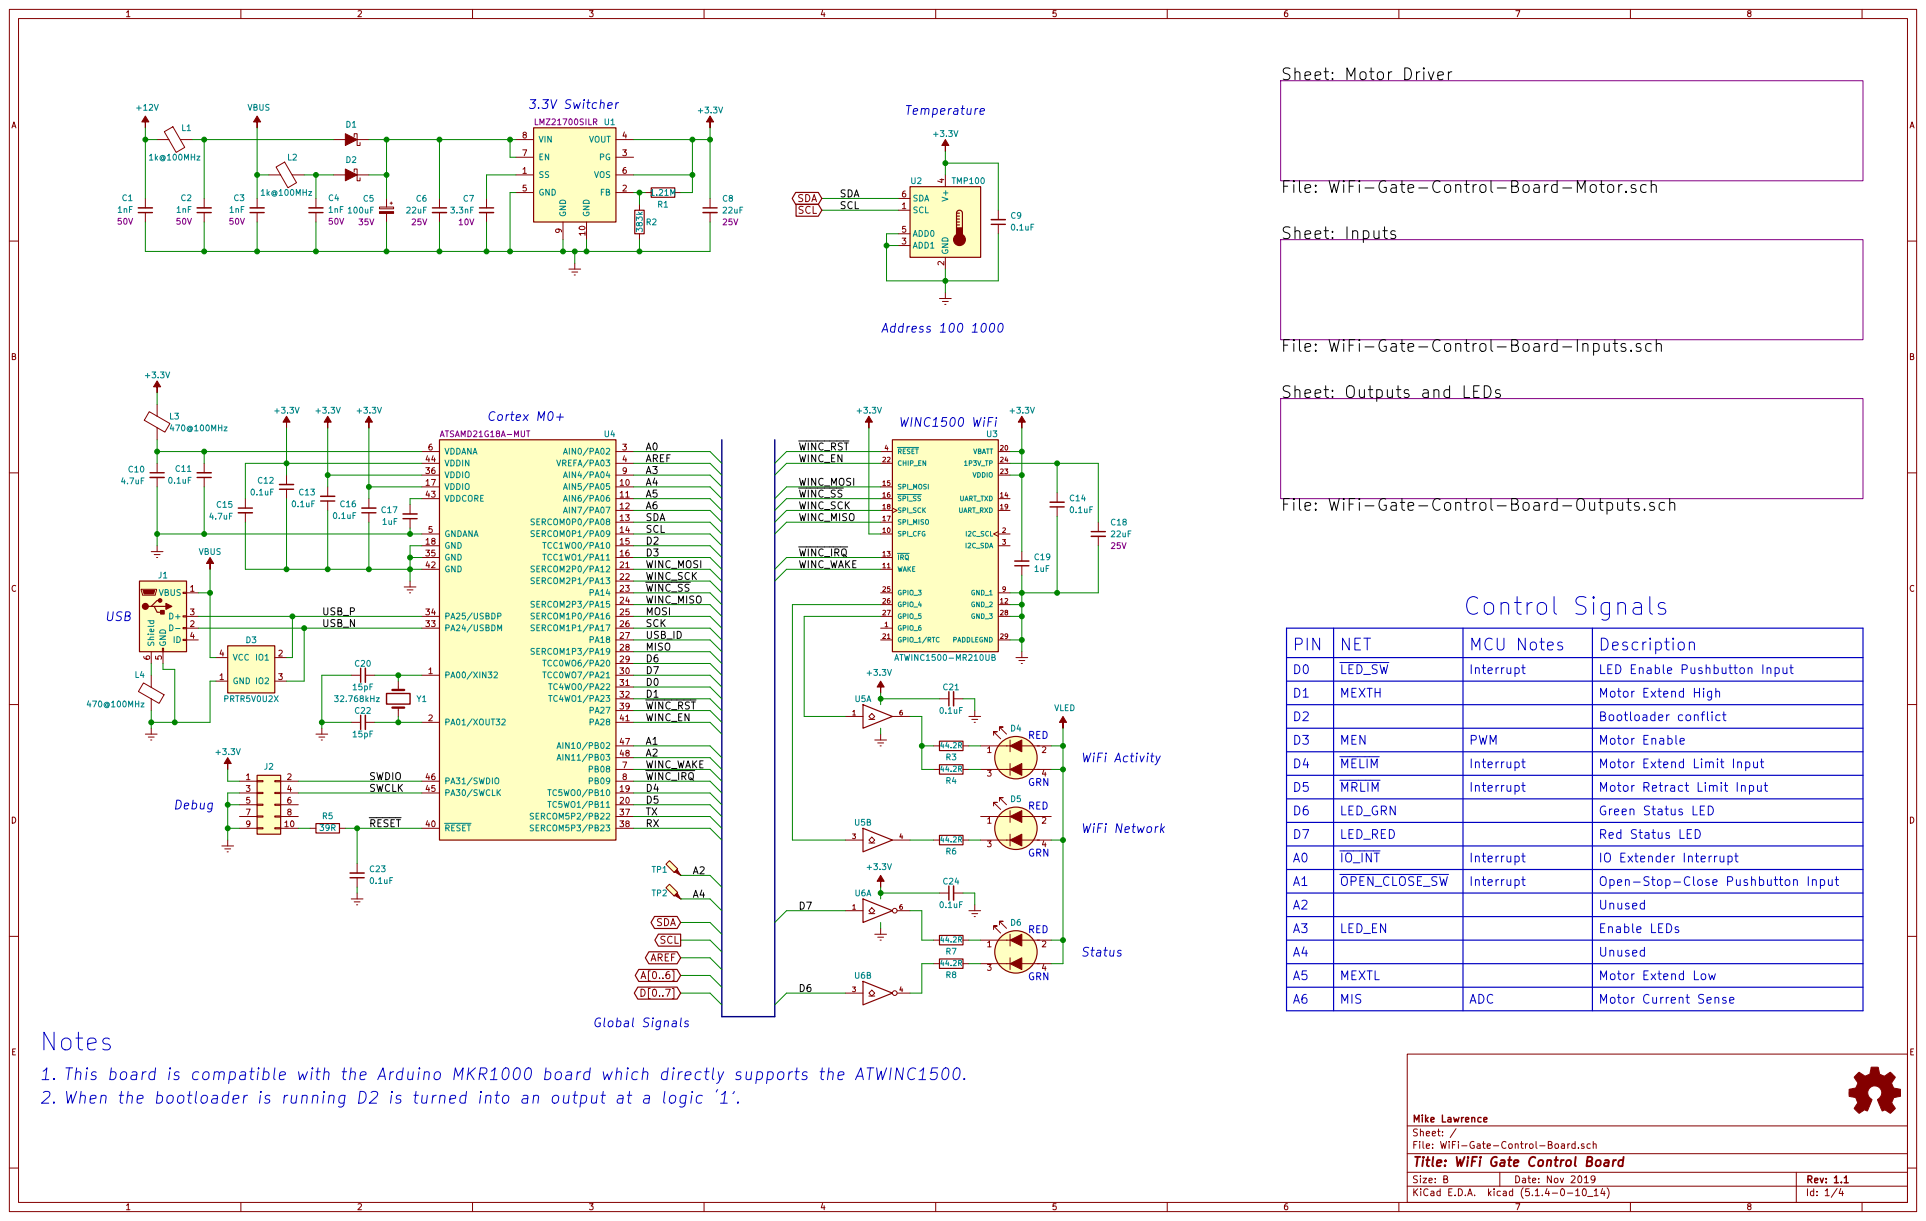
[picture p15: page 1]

4 ADD0 5 SDA 6 U2 TMP100 SS 1 GND 10 FB 2 PG 3 VOUT 4 GND 5 VOS 6 EN 7 VIN 8 GND

File: WiFi-Gate-Control-Board-Motor.sch

File: WiFi-Gate-Control-Board-Inputs.sch

Sheet: Outputs and LEDs

File: WiFi-Gate-Control-Board-Outputs.sch

USB_N

MCU Notes

D0
D1
D2 | | Bootloader conflict
D3 | MEN | | Motor Enable
D4

Motor Retract Limit Input

A0
A1
A2
A3
A4

Notes
This board is compatible with the Arduino MKR1000 board which directly supports the ATWINC1500.

When the bootloader is running D2 is turned into an output at a logic 1.

File: WiFi-Gate-Control-Board.sch Sheet: / Mike Lawrence

Id: 1/4 Title: WiFi Gate Control Board

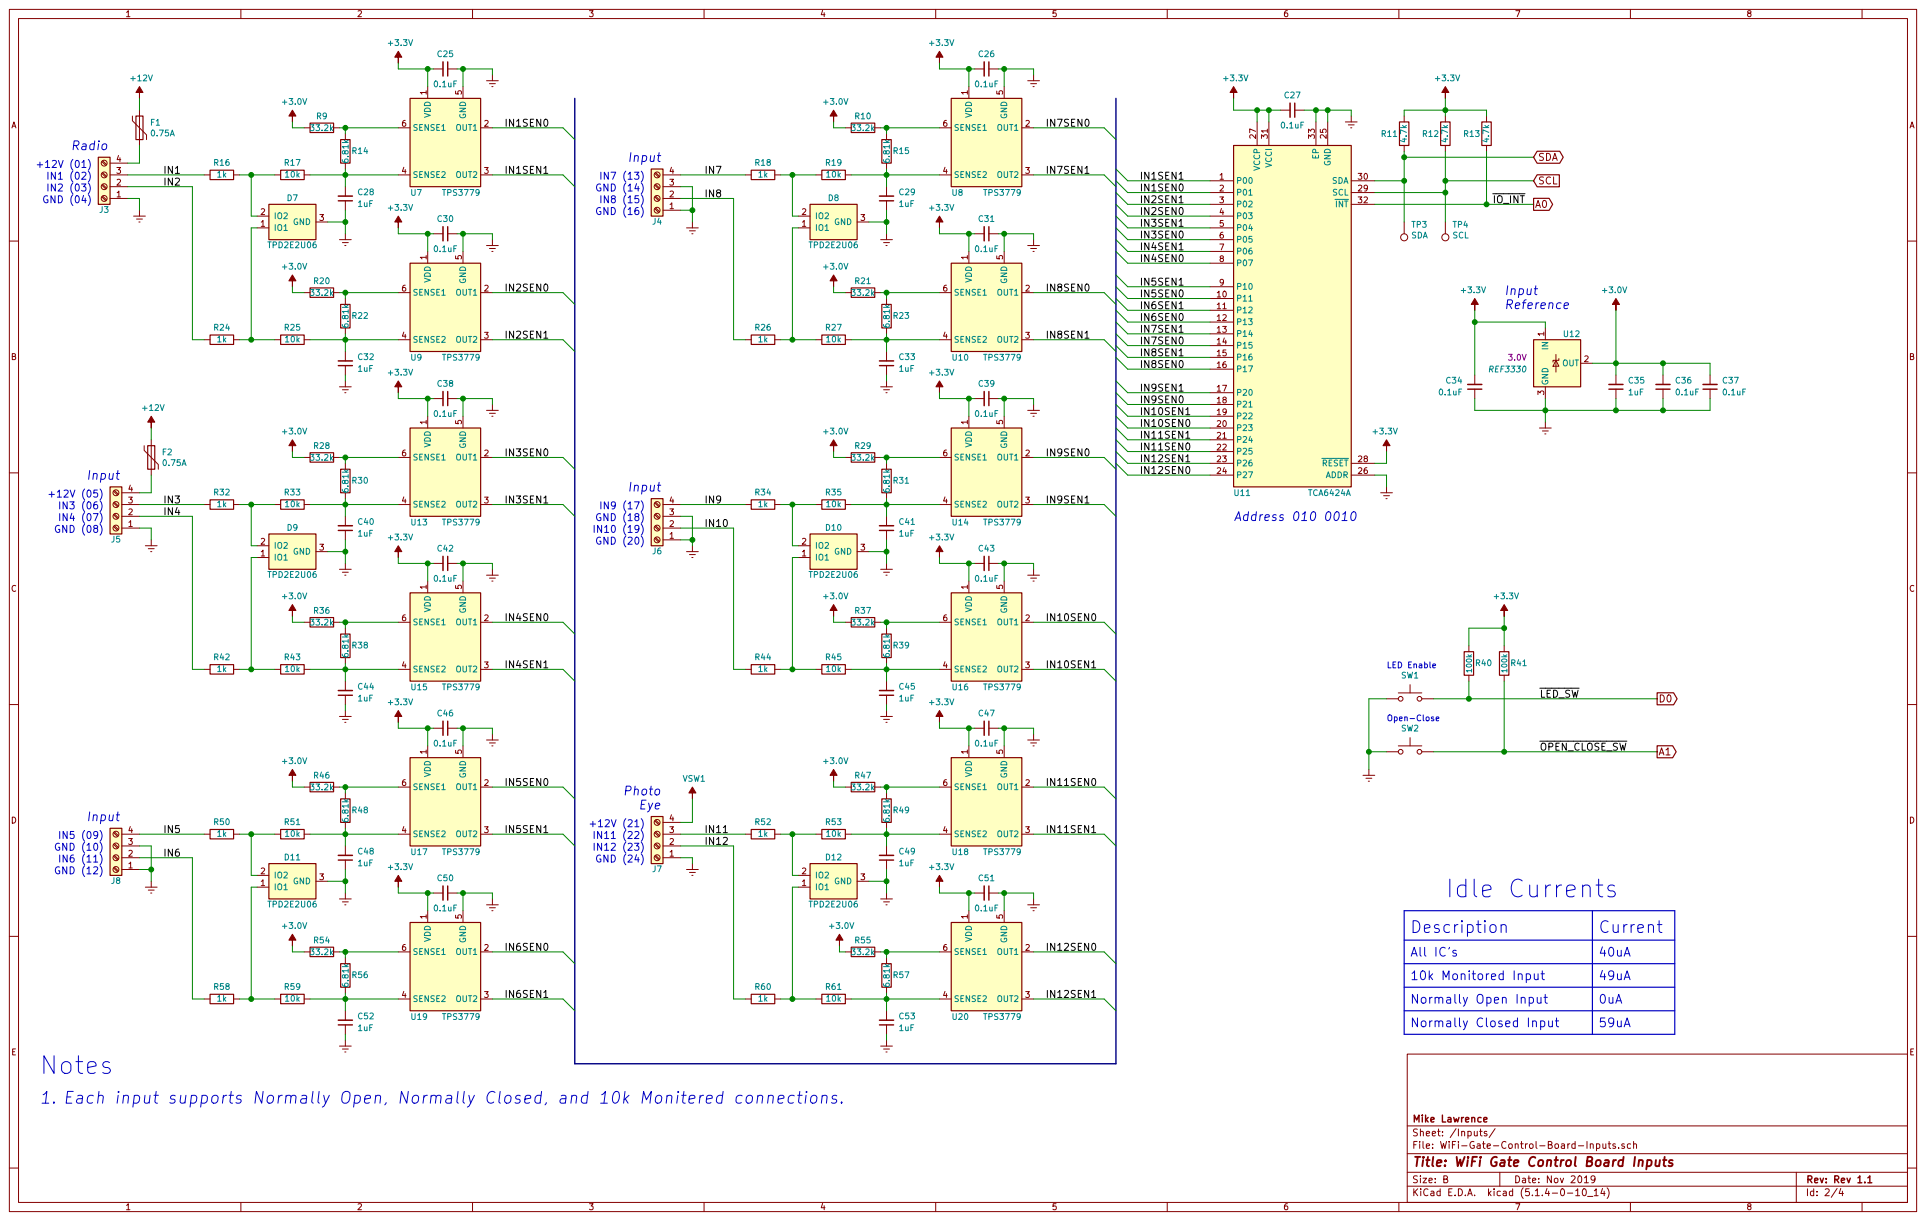
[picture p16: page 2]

Current

All ICs | 40uA

49uA
0uA
59uA

Each input supports Normally Open, Normally Closed, and 10k Monitered connections.

Sheet: /Inputs/ Mike Lawrence

File: WiFi-Gate-Control-Board-Inputs.sch
Id: 2/4 Title: WiFi Gate Control Board Inputs

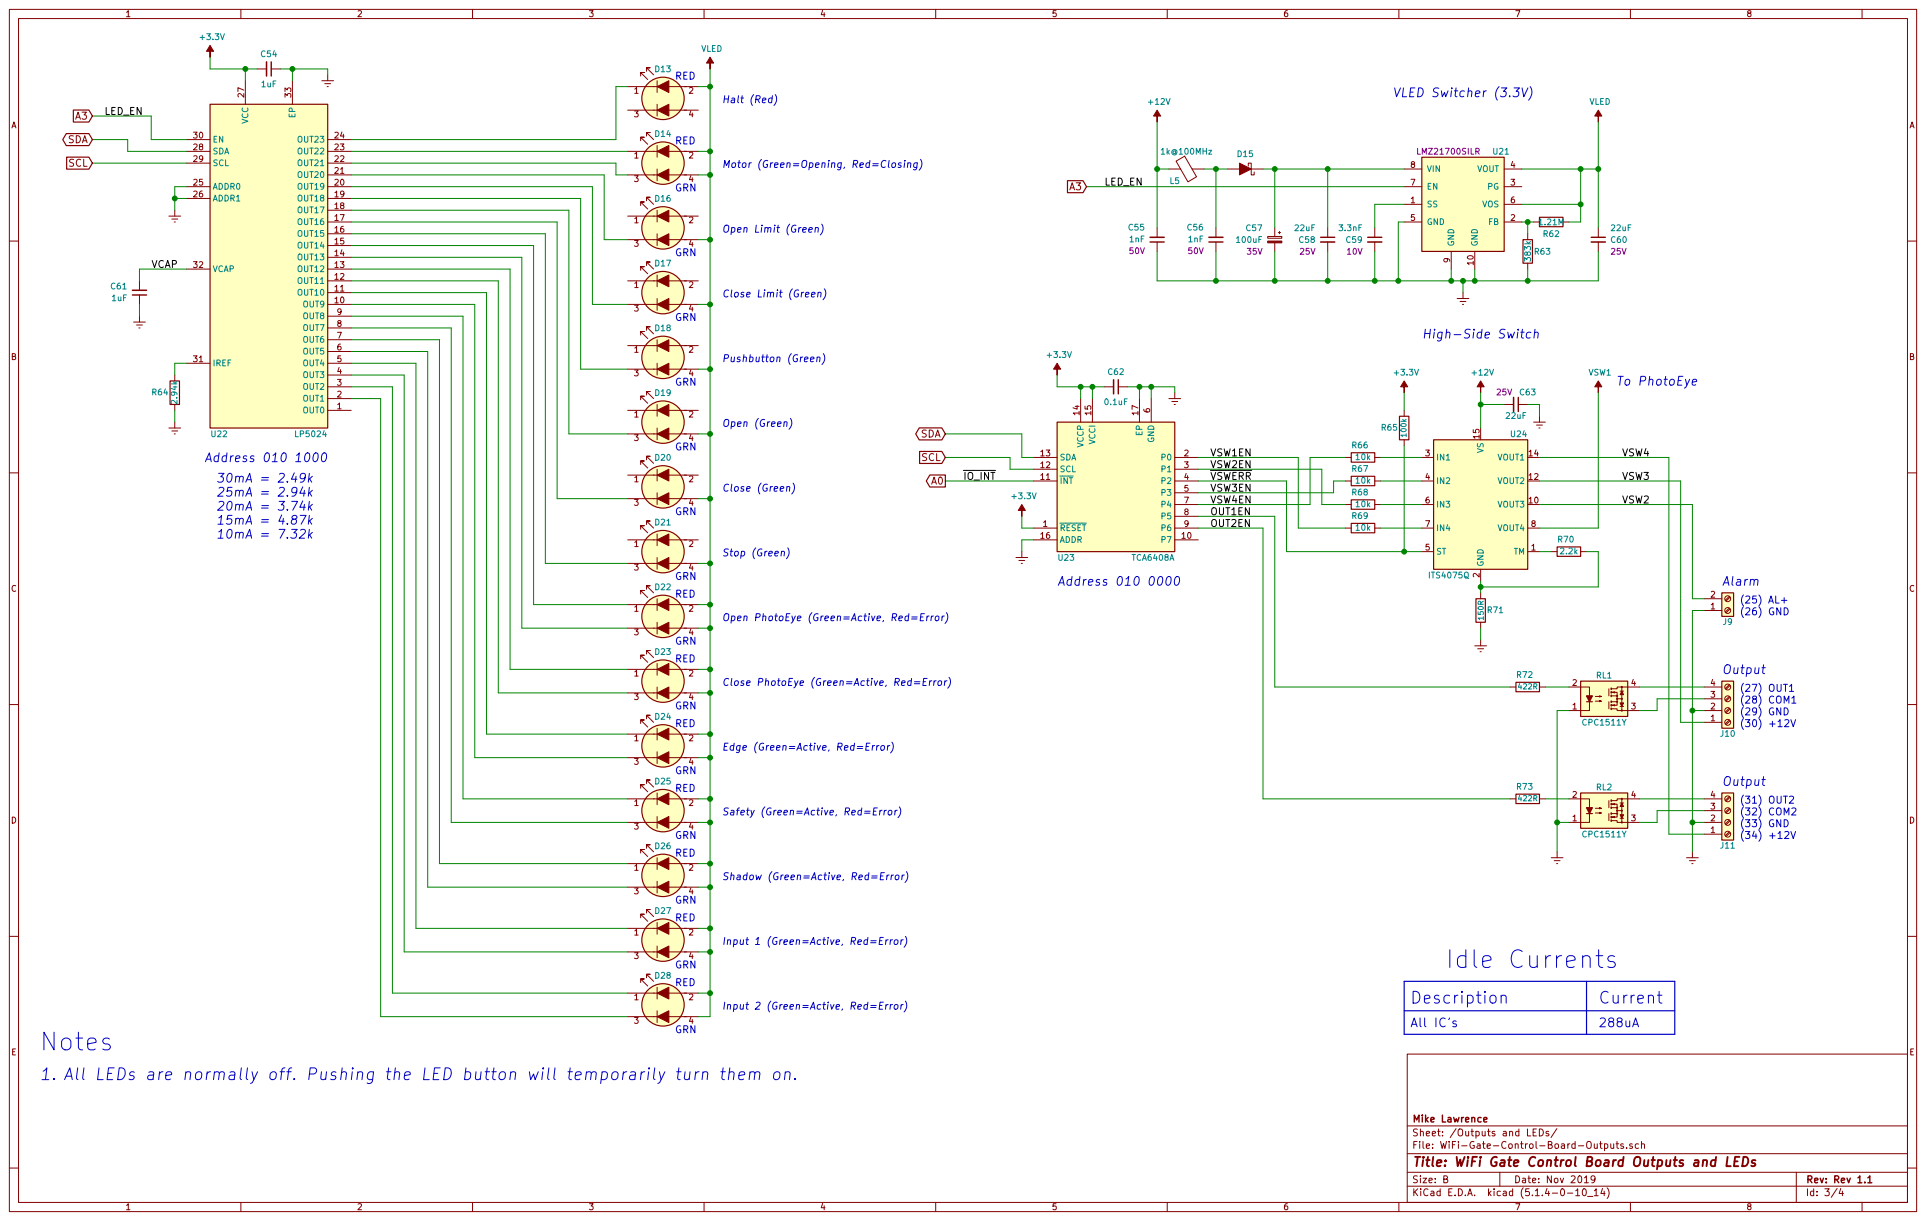
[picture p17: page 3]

Motor (Green=Opening, Red=Closing)

VSW4EN
OUT1EN
OUT2EN

Close PhotoEye (Green=Active, Red=Error)

RED All LEDs are normally off. Pushing the LED button will temporarily turn them on.

Edge (Green=Active, Red=Error)

Safety (Green=Active, Red=Error)

Shadow (Green=Active, Red=Error)

Input 1 (Green=Active, Red=Error)

Input 2 (Green=Active, Red=Error)

Sheet: /Outputs and LEDs/ Mike Lawrence

File: WiFi-Gate-Control-Board-Outputs.sch
Id: 3/4 Title: WiFi Gate Control Board Outputs and LEDs

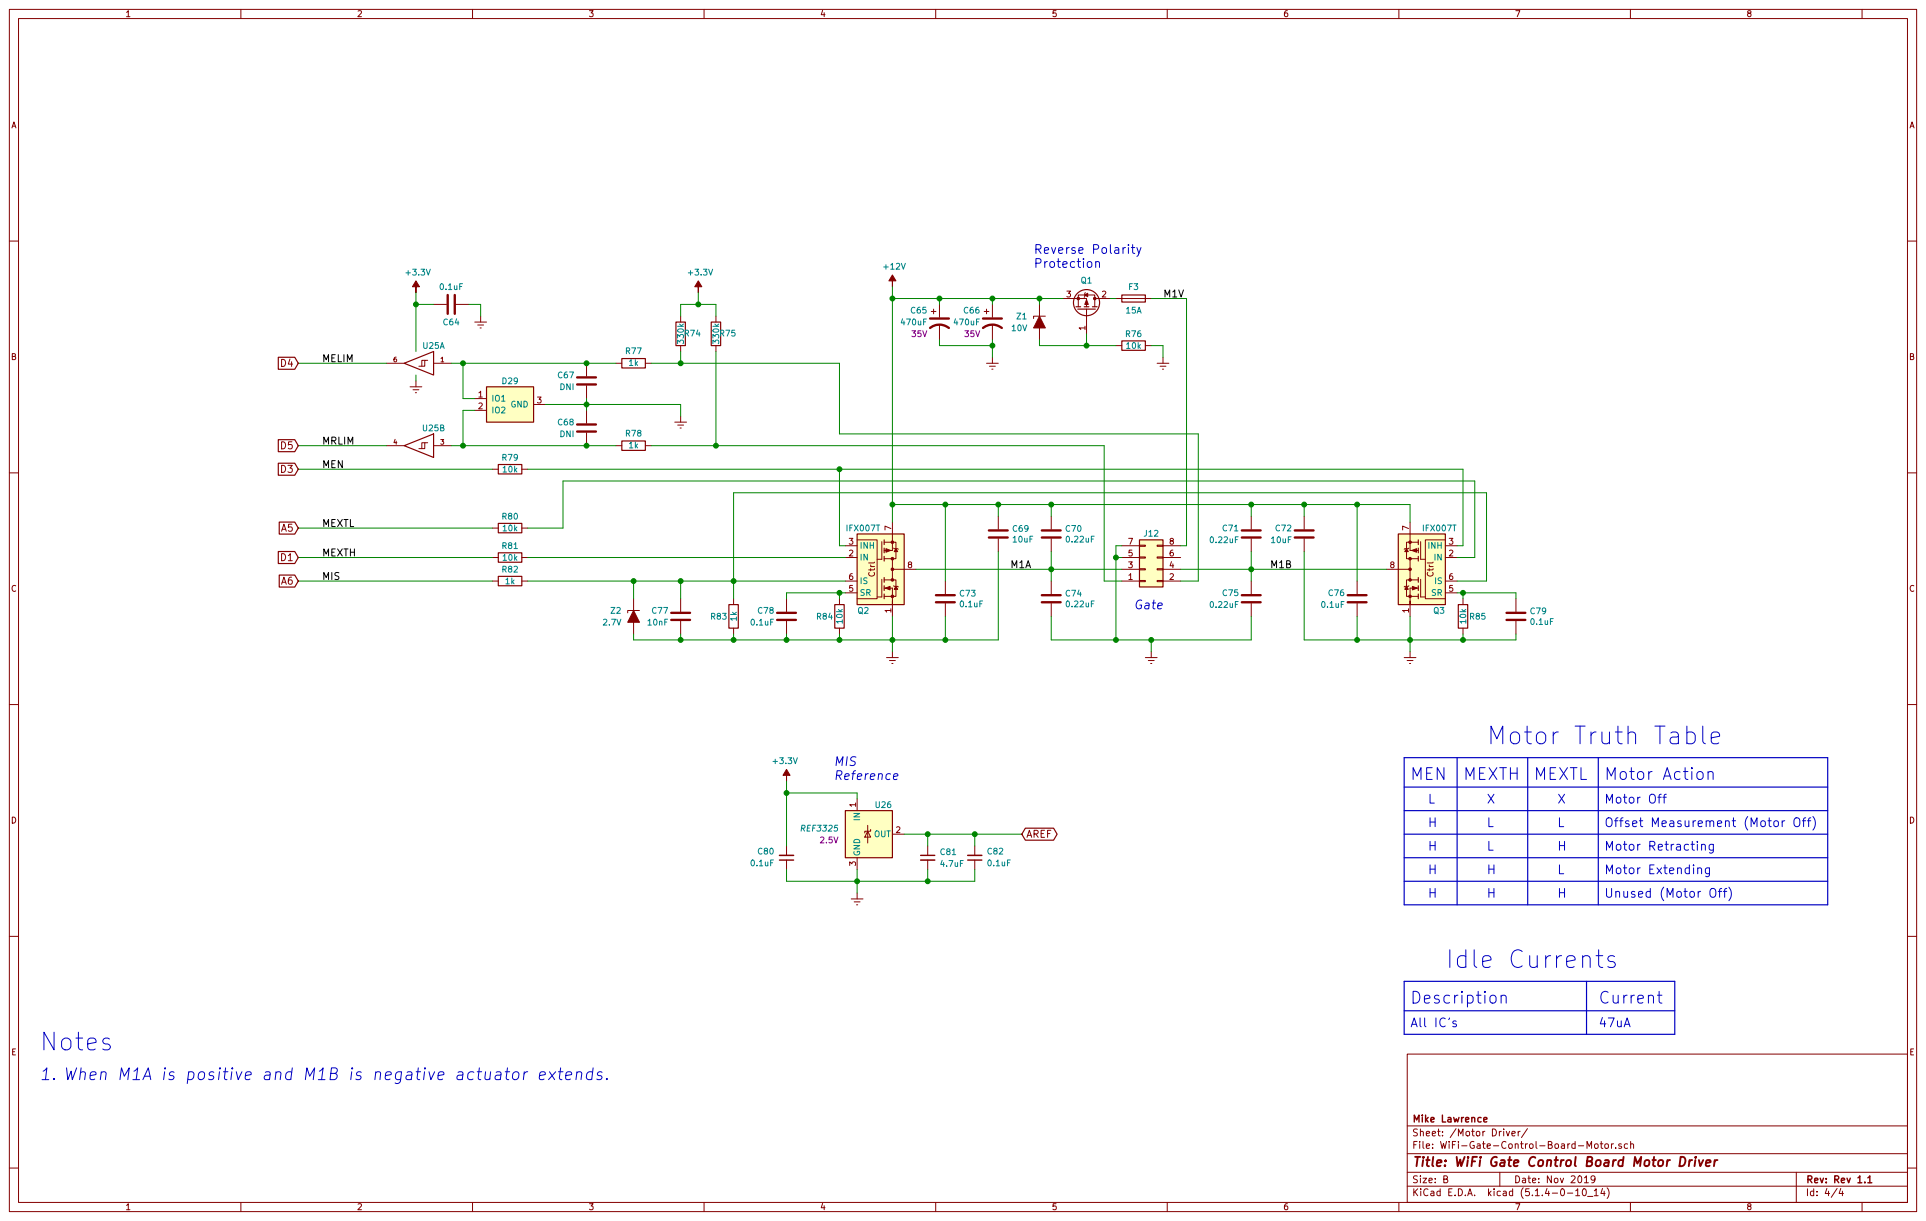
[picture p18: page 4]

MEN | MEXTH

X | X | | Motor Off

Offset Measurement (Motor Off)
Motor Retracting

Notes
1. When M1A is positive and M1B is negative actuator extends.

Id: 4/4 Title: WiFi Gate Control Board Motor Driver File: WiFi-Gate-Control-Board-Motor.sch Sheet: /Motor Driver/ Mike Lawrence

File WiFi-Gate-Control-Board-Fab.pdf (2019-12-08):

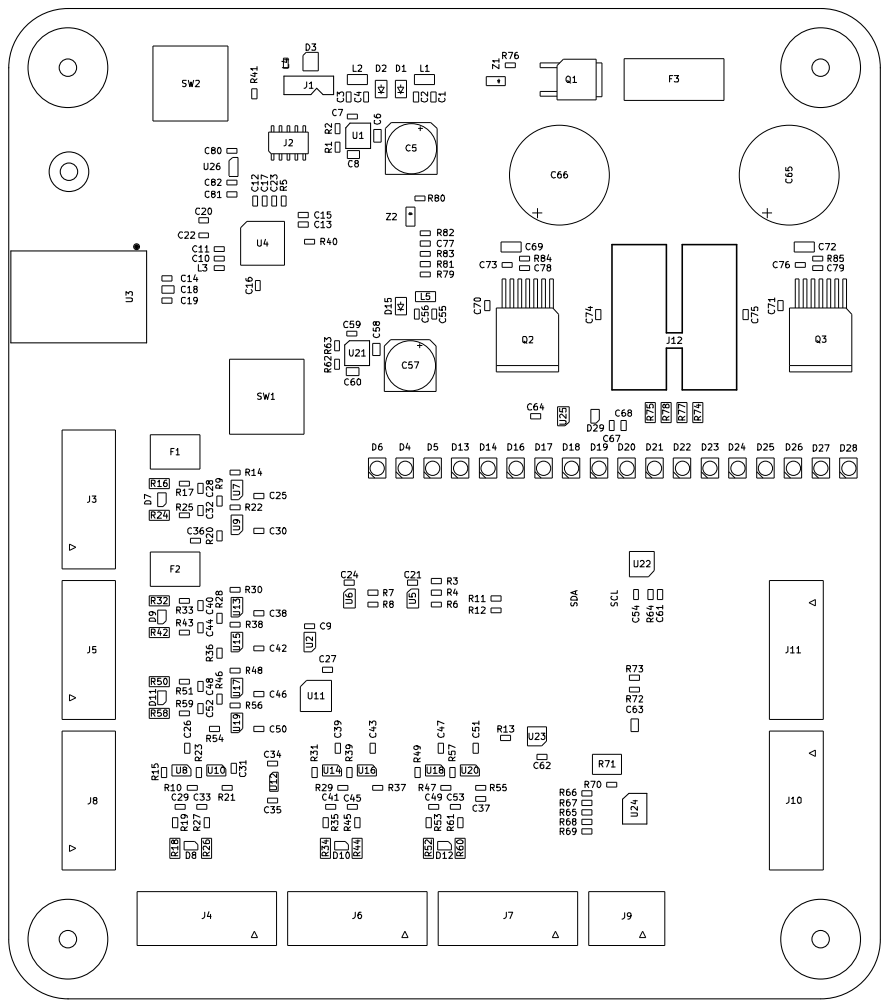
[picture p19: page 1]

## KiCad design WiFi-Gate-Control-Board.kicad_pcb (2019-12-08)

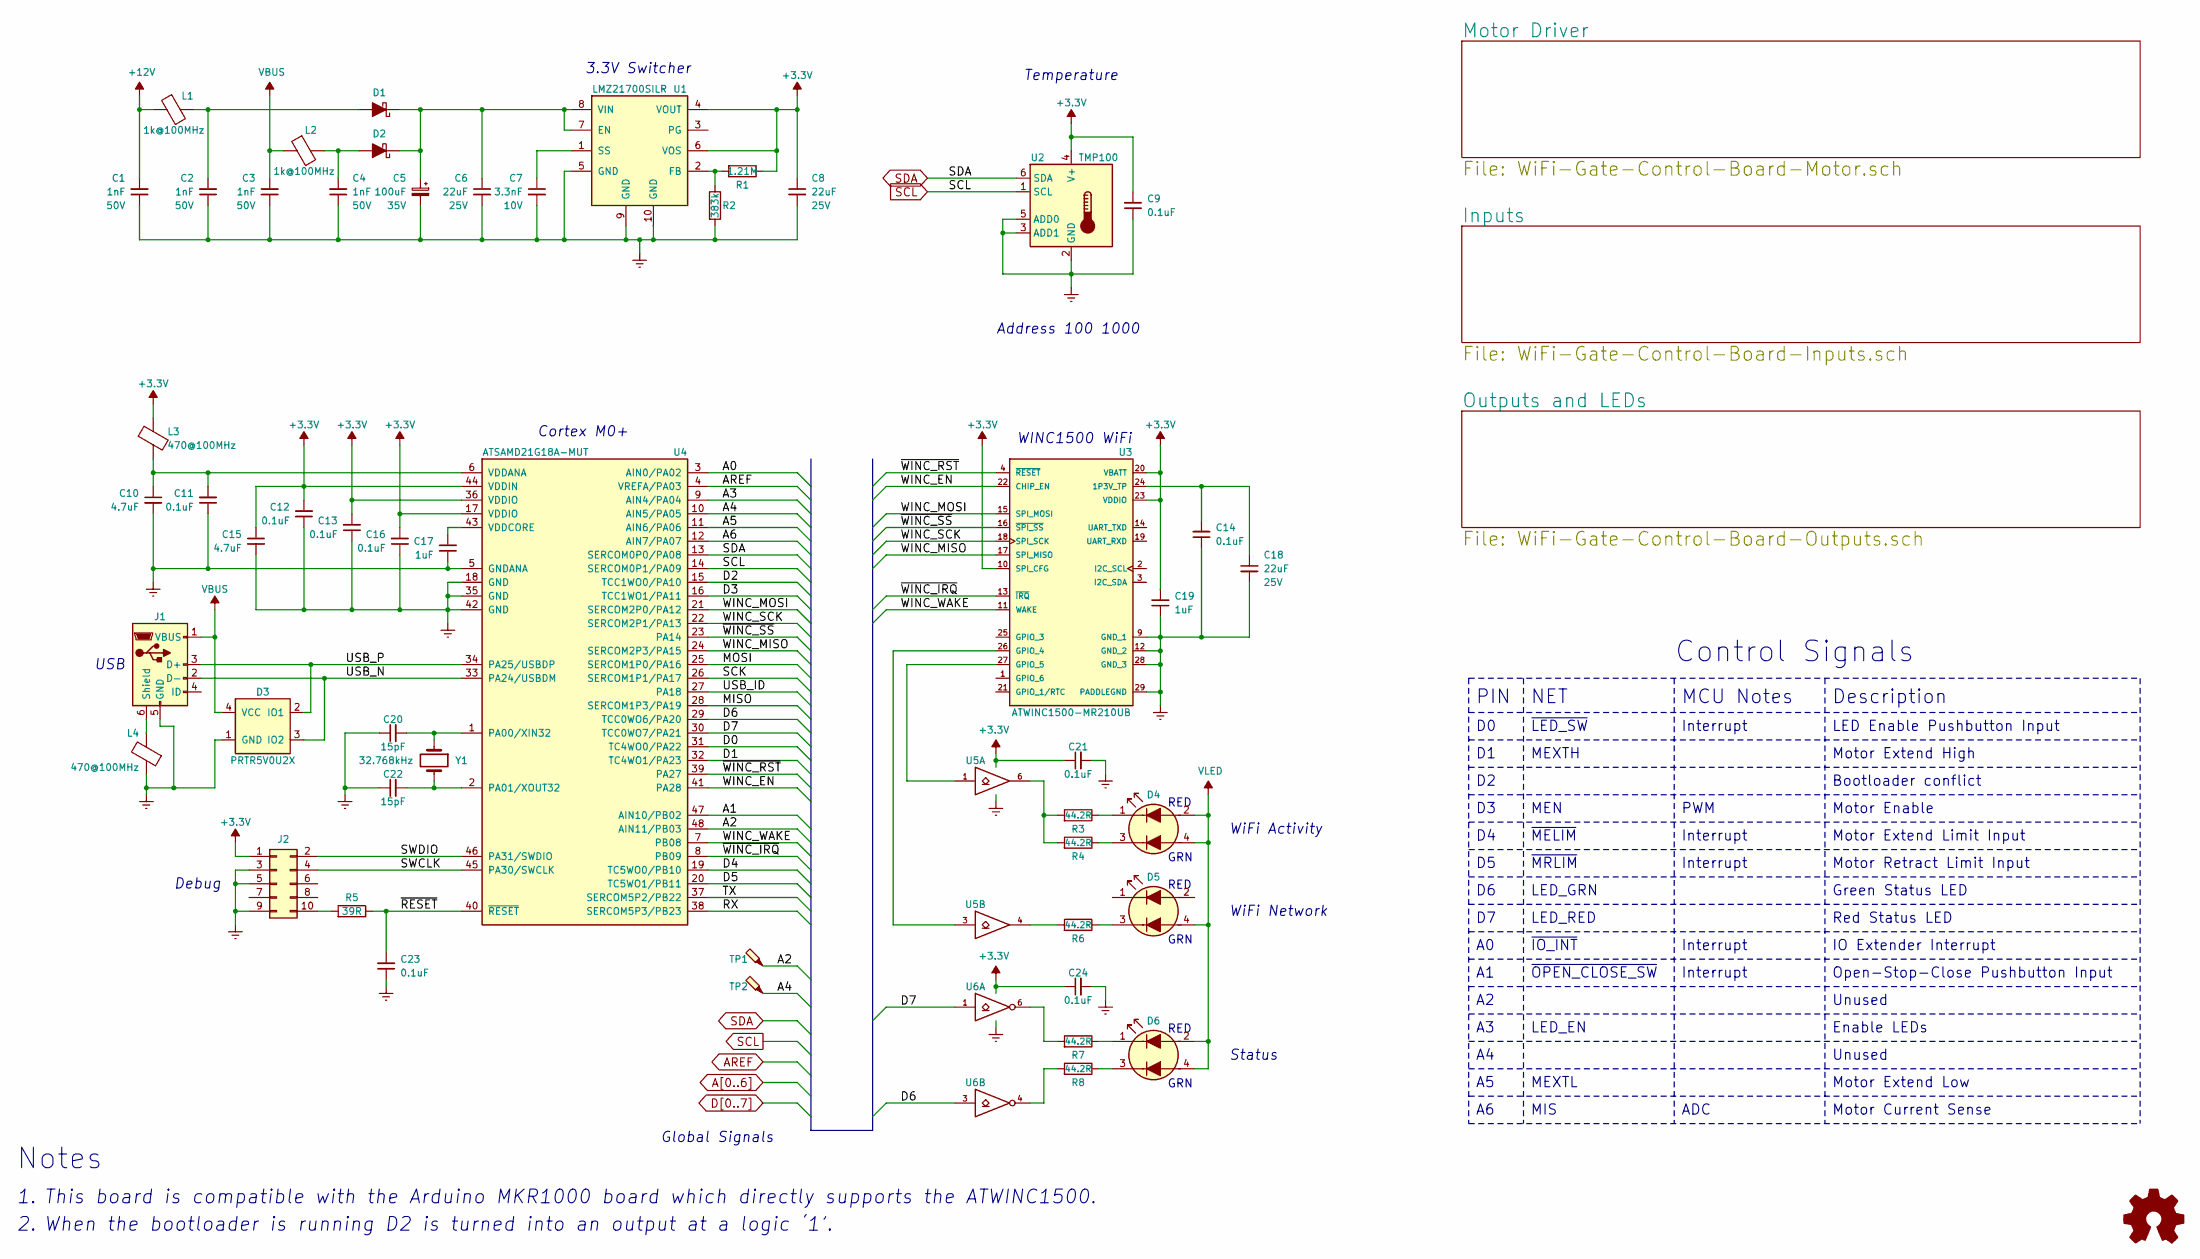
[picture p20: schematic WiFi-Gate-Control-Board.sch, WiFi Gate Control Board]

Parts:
C1, C2, C3, C4: 1nF; C_0603_1608Metric; Voltage 50V; Tolerance 10%; Part Number VJ0603Y102KXAAC31
C5: 100uF; CP_Elec_8x10; Voltage 35V; Tolerance 20%; Part Number EMVH350ADA101MHA0G
C6, C8, C18: 22uF; C_0805_2012Metric; Voltage 25V; Tolerance 20%; Part Number TMK212BBJ226MG-TT
C7: 3.3nF; C_0603_1608Metric; Voltage 10V; Tolerance 5%; Part Number VJ0603Y332JXQPW1BC
C9, C11, C12, C13, C14, C16, C21, C23, C24: 0.1uF; C_0603_1608Metric; Voltage 50V; Tolerance 5%; Part Number CC603JRX7R9BB104
C10, C15: 4.7uF; C_0603_1608Metric; Voltage 6.3V; Tolerance 10%; Part Number JMK107BB7475KA-T
C17, C19: 1uF; C_0603_1608Metric; Voltage 50V; Tolerance 10%; Part Number UMK107BJ105KA-T
C20, C22: 15pF; C_0603_1608Metric; Voltage 50V; Tolerance 5%; Part Number 06035A150JAT2A
D1, D2: DFLS130; D_PowerDI-123; Part Number DFLS130LQ
D3: PRTR5V0U2X; SOT-143; Part Number PRTR5V0U2X,215
D4, D5, D6: Red/Green; LED_Avago_PLCC4_3.2x2.8mm_CW; Part Number HSMF-A203-A00J1
J1: USB_B_Micro; USB_Micro-B_Wuerth_614105150721_Vertical_CircularHoles; Part Number 614105150721
J2: Cortex Debug; PinHeader_2x05_P1.27mm_Vertical_SMD; Part Number FTSH-105-01-L-DV-K
L1, L2: 1k@100MHz; L_1206_3216Metric; Part Number BLM31KN102SH1L
L3, L4: 470@100MHz; L_0603_1608Metric; Part Number BLM18PG471SN1D
R1: 1.21M; R_0603_1608Metric; Tolerance 1%; Part Number RC0603FR-071M21L
R2: 383k; R_0603_1608Metric; Tolerance 1%; Part Number ERJ-3EKF3833V
R3, R4, R6, R7, R8: 44.2R; R_0603_1608Metric; Tolerance 1%; Part Number ERJ-3EKF44R2V
R5: 39R; R_0603_1608Metric; Tolerance 1%; Part Number ERJ-3EKF39R0V
TP1, TP2: TestPoint_Probe; TestPoint_Pad_D1.0mm
U1: LMZ21700; Converter_DCDC_Texas-SIL0008E; Part Number LMZ21700SILR
U2: TMP100; SOT-23-6; Part Number TMP100AQDBVRQ1
U3: ATWINC1500-MR210UB; Microchip_ATWINC1500-MR210UB; Part Number ATWINC1500-MR210UB1140
U4: SAMD21G18-M; QFN-48-1EP_7x7mm_P0.5mm_EP5.15x5.15mm; Part Number ATSAMD21G18A-MUT
U5: 74LVC2G07; SOT-23-6; Part Number SN74LVC2G07DBVR
U6: 74LVC2G06; SOT-23-6; Part Number SN74LVC2G06DBVR
Y1: 32.768kHz; Crystal_SMD_Abracon_ABS07-2Pin_3.2x1.5mm; Part Number ABS07-32.768KHZ-9-T

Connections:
+3.3V: C8.1, C9.2, C12.2, C13.2, C15.1, C16.2, C19.2, C21.1, C24.1, J2.1, L3.1, R1.1, U1.4 (VOUT), U1.6 (VOS), U2.4 (V+), U3.10 (SPI_CFG), U3.20 (VBATT), U3.23 (VDDIO), U4.17 (VDDIO), U4.36 (VDDIO), U4.44 (VDDIN), U5.5 (VCC), U6.5 (VCC); also elsewhere on the board
+12V: C1.2, L1.1; also elsewhere on the board
/SWCLK: J2.4, U4.45 (PA30/SWCLK)
/SWDIO: J2.2, U4.46 (PA31/SWDIO)
/USB_N: D3.3 (IO2), J1.2 (D-), U4.33 (PA24/USBDM)
/USB_P: D3.2 (IO1), J1.3 (D+), U4.34 (PA25/USBDP)
/WINC_EN: U3.22 (CHIP_EN), U4.41 (PA28)
/WINC_MISO: U3.17 (SPI_MISO), U4.24 (SERCOM2P3/PA15)
/WINC_MOSI: U3.15 (SPI_MOSI), U4.21 (SERCOM2P0/PA12)
/WINC_SCK: U3.18 (SPI_SCK), U4.22 (SERCOM2P1/PA13)
/WINC_WAKE: U3.11 (WAKE), U4.7 (PB08)
/~RESET~: C23.2, R5.1, U4.40 (~RESET~)
/~WINC_IRQ: U3.13 (~IRQ~), U4.8 (PB09)
/~WINC_RST: U3.4 (~RESET~), U4.39 (PA27)
/~WINC_SS: U3.16 (~SPI_SS~), U4.23 (PA14)
A0: U4.3 (AIN0/PA02); also elsewhere on the board
A1: U4.47 (AIN10/PB02); also elsewhere on the board
A2: TP1.1, U4.48 (AIN11/PB03)
A3: U4.9 (AIN4/PA04); also elsewhere on the board
A4: TP2.1, U4.10 (AIN5/PA05)
A5: U4.11 (AIN6/PA06); also elsewhere on the board
A6: U4.12 (AIN7/PA07); also elsewhere on the board
AREF: U4.4 (VREFA/PA03); also elsewhere on the board
D0: U4.31 (TC4WO0/PA22); also elsewhere on the board
D1: U4.32 (TC4WO1/PA23); also elsewhere on the board
D3: U4.16 (TCC1WO1/PA11); also elsewhere on the board
D4: U4.19 (TC5WO0/PB10); also elsewhere on the board
D5: U4.20 (TC5WO1/PB11); also elsewhere on the board
D6: U4.29 (TCC0WO6/PA20), U6.3
D7: U4.30 (TCC0WO7/PA21), U6.1
GND: C1.1, C2.1, C3.1, C4.1, C5.2, C6.2, C7.2, C8.2, C9.1, C10.2, C11.1, C12.1, C13.1, C14.1, C15.2, C16.1, C17.1, C18.2, C19.1, C20.1, C21.2, C22.1, C23.1, C24.2, D3.1 (GND), J1.5 (GND), J2.3, J2.5, J2.9, L4.1, R2.2, U1.5 (GND), U1.9 (GND), U1.10 (GND), U2.2 (GND), U2.3 (ADD1), U2.5 (ADD0), U3.9 (GND_1), U3.12 (GND_2), U3.28 (GND_3), U3.29 (PADDLEGND), U4.5 (GNDANA), U4.18 (GND), U4.35 (GND), U4.42 (GND), U5.2 (GND), U6.2 (GND); also elsewhere on the board
unnamed: C2.2, D1.2 (A), L1.2
unnamed: C4.2, D2.2 (A), L2.2
unnamed: C5.1, C6.1, D1.1 (K), D2.1 (K), U1.7 (EN), U1.8 (VIN)
unnamed: C7.1, U1.1 (SS)
unnamed: C10.1, C11.2, L3.2, U4.6 (VDDANA)
unnamed: C14.2, C18.1, U3.24 (1P3V_TP)
unnamed: C17.2, U4.43 (VDDCORE)
unnamed: C20.2, U4.1 (PA00/XIN32), Y1.1
unnamed: C22.2, U4.2 (PA01/XOUT32), Y1.2
unnamed: D4.1 (K1), R3.1
unnamed: D4.3 (K2), R4.1
unnamed: D5.3 (K2), R6.1
unnamed: D6.1 (K1), R7.1
unnamed: D6.3 (K2), R8.1
unnamed: J1.6 (Shield), L4.2
unnamed: J2.10, R5.2
unnamed: R1.2, R2.1, U1.2 (FB)
unnamed: R3.2, R4.2, U5.6
unnamed: R6.2, U5.4
unnamed: R7.2, U6.6
unnamed: R8.2, U6.4
unnamed: U3.26 (GPIO_4), U5.3
unnamed: U3.27 (GPIO_5), U5.1
SCL: U2.1 (SCL), U4.14 (SERCOM0P1/PA09); also elsewhere on the board
SDA: U2.6 (SDA), U4.13 (SERCOM0P0/PA08); also elsewhere on the board
VBUS: C3.2, D3.4 (VCC), J1.1 (VBUS), L2.1
VLED: D4.2 (A1), D4.4 (A2), D5.4 (A2), D6.2 (A1), D6.4 (A2); also elsewhere on the board

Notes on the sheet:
3.3V Switcher
Temperature
This board is compatible with the Arduino MKR1000 board which directly supports the ATWINC1500.
Debug
USB
Cortex M0+
WINC1500 WiFi
When the bootloader is running D2 is turned into an output at a logic ‘1’.
Global Signals
Status
RED
GRN
WiFi Activity
WiFi Network
~OPEN_CLOSE_SW
Open-Stop-Close Pushbutton Input
~IO_INT
IO Extender Interrupt
~MELIM
Motor Extend Limit Input
LED_GRN
Green Status LED
LED_RED
Red Status LED
Motor Current Sense
MEXTH
Motor Extend High
PIN
NET
Description
Bootloader conflict
Control Signals
LED_EN
Enable LEDs
MCU Notes
Interrupt
ADC
Motor Extend Low
MIS
LED Enable Pushbutton Input

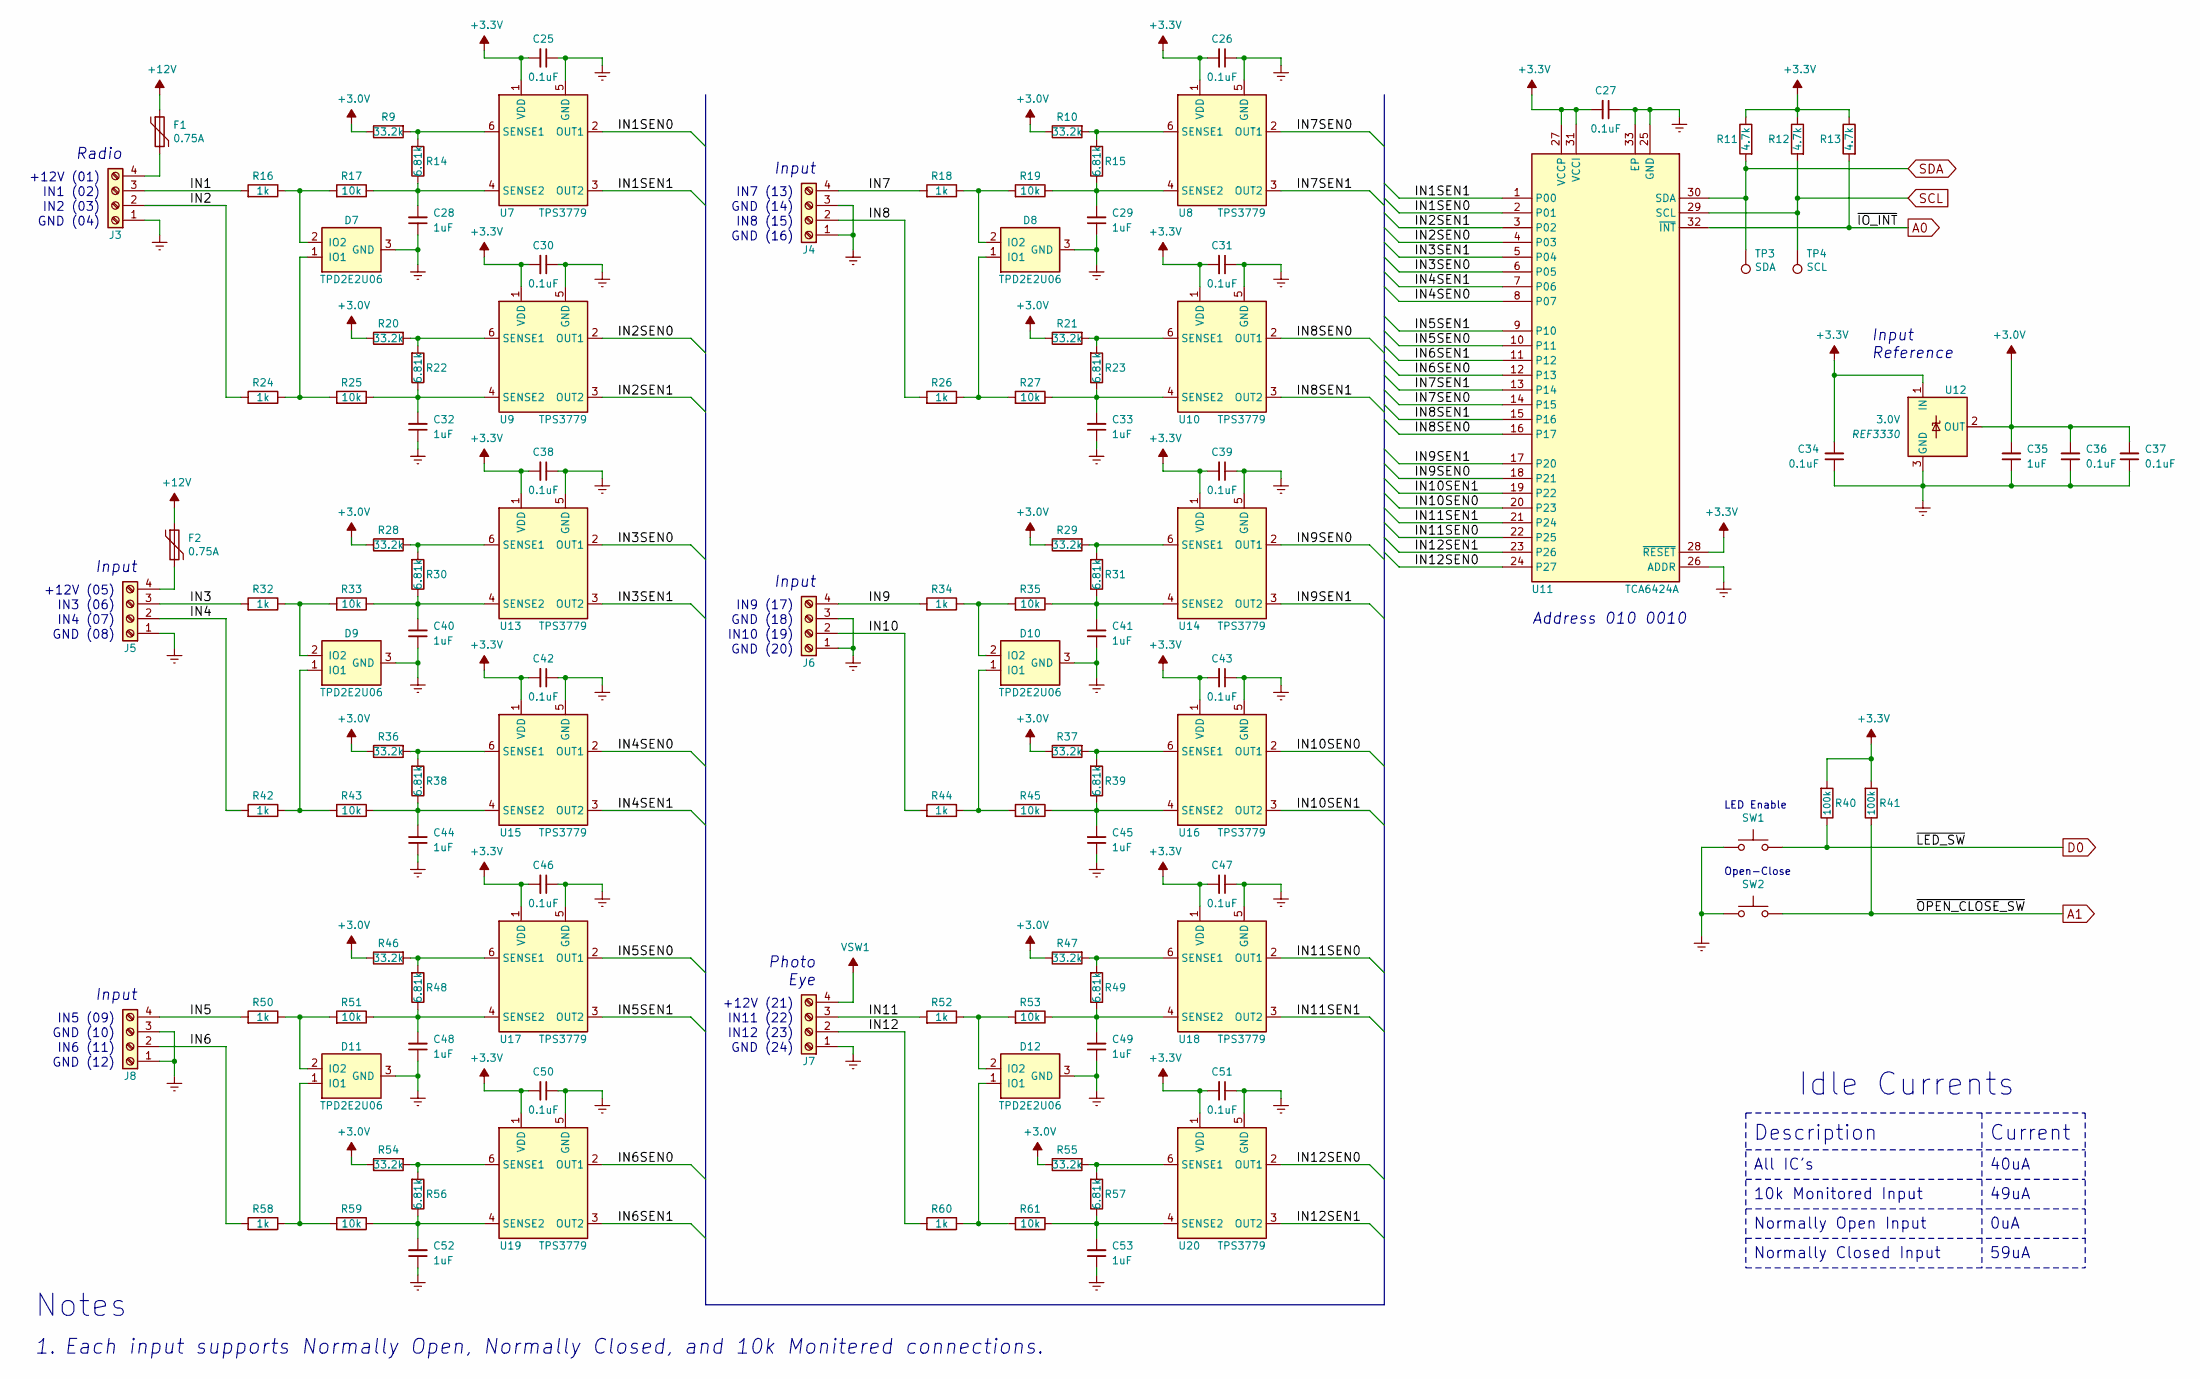
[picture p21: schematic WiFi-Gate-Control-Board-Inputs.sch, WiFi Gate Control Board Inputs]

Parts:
C25, C26, C27, C30, C31, C34, C36, C37, C38, C39, C42, C43, C46, C47, C50, C51: 0.1uF; C_0603_1608Metric; Voltage 50V; Tolerance 5%; Part Number CC603JRX7R9BB104
C28, C29, C32, C33, C35, C40, C41, C44, C45, C48, C49, C52, C53: 1uF; C_0603_1608Metric; Voltage 50V; Tolerance 10%; Part Number UMK107BJ105KA-T
D7, D8, D9, D10, D11, D12: TPD2E2U06; SOT-323_SC-70; Part Number TPD2E2U06QDCKRQ1
F1, F2: 0.75A; Fuse_Bourns_MF-SM_7.98x5.44mm; Part Number MFSM075-2
J3, J4, J5, J6, J7, J8: Screw Header 4 Pos; PhoenixContact_MSTBVA_2,5_4-G-5,08_1x04_P5.08mm_Vertical; Part Number 1755752
R9, R10, R20, R21, R28, R29, R36, R37, R46, R47, R54, R55: 33.2k; R_0603_1608Metric; Tolerance 0.5%; Part Number RR0816P-3322D51C
R11, R12, R13: 4.7k; R_0603_1608Metric; Tolerance 1%; Part Number ERJ-3EKF4701V
R14, R15, R22, R23, R30, R31, R38, R39, R48, R49, R56, R57: 6.81k; R_0603_1608Metric; Tolerance 0.5%; Part Number RR0816P-6811D81H
R16, R18, R24, R26, R32, R34, R42, R44, R50, R52, R58, R60: 1k; R_1206_3216Metric; Tolerance 0.5%; Part Number AC1206DR-071KL
R17, R19, R25, R27, R33, R35, R43, R45, R51, R53, R59, R61: 10k; R_0603_1608Metric; Tolerance 0.5%; Part Number RR0816P-103-D
R40, R41: 100k; R_0603_1608Metric; Tolerance 1%; Part Number ERJ-3EKF1003V
SW1, SW2: SW_PUSH-12mm_Wuerth-430476085716; Part Number 430476085716
TP3: SDA; TestPoint_THTPad_D1.5mm_Drill0.7mm
TP4: SCL; TestPoint_THTPad_D1.5mm_Drill0.7mm
U7, U8, U9, U10, U13, U14, U15, U16, U17, U18, U19, U20: TPS3779; SOT-23-6; Part Number TPS3779BDBVR
U11: TCA6424A; VQFN-32-1EP_5x5mm_P0.5mm_EP3.1x3.1mm_ThermalVias; Part Number TCA6424ARGJR
U12: REF3330; SOT-23; Voltage 3.0V; Part Number REF3330AIDBZR

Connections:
+3.0V: C35.2, C36.2, C37.2, R9.1, R10.1, R20.1, R21.1, R28.1, R29.1, R36.1, R37.1, R46.1, R47.1, R54.1, R55.1, U12.2 (OUT)
+3.3V: C25.2, C26.2, C27.2, C30.2, C31.2, C34.2, C38.2, C39.2, C42.2, C43.2, C46.2, C47.2, C50.2, C51.2, R11.1, R12.1, R13.1, R40.2, R41.2, U7.1 (VDD), U8.1 (VDD), U9.1 (VDD), U10.1 (VDD), U11.27 (VCCP), U11.28 (~RESET), U11.31 (VCCI), U12.1 (IN), U13.1 (VDD), U14.1 (VDD), U15.1 (VDD), U16.1 (VDD), U17.1 (VDD), U18.1 (VDD), U19.1 (VDD), U20.1 (VDD); also elsewhere on the board
+12V: F1.1, F2.1; also elsewhere on the board
/Inputs/IN1: J3.3, R16.2
/Inputs/IN1SEN0: U7.2 (OUT1), U11.2 (P01)
/Inputs/IN1SEN1: U7.3 (OUT2), U11.1 (P00)
/Inputs/IN2: J3.2, R24.2
/Inputs/IN2SEN0: U9.2 (OUT1), U11.4 (P03)
/Inputs/IN2SEN1: U9.3 (OUT2), U11.3 (P02)
/Inputs/IN3: J5.3, R32.2
/Inputs/IN3SEN0: U11.6 (P05), U13.2 (OUT1)
/Inputs/IN3SEN1: U11.5 (P04), U13.3 (OUT2)
/Inputs/IN4: J5.2, R42.2
/Inputs/IN4SEN0: U11.8 (P07), U15.2 (OUT1)
/Inputs/IN4SEN1: U11.7 (P06), U15.3 (OUT2)
/Inputs/IN5: J8.4, R50.2
/Inputs/IN5SEN0: U11.10 (P11), U17.2 (OUT1)
/Inputs/IN5SEN1: U11.9 (P10), U17.3 (OUT2)
/Inputs/IN6: J8.2, R58.2
/Inputs/IN6SEN0: U11.12 (P13), U19.2 (OUT1)
/Inputs/IN6SEN1: U11.11 (P12), U19.3 (OUT2)
/Inputs/IN7: J4.4, R18.2
/Inputs/IN7SEN0: U8.2 (OUT1), U11.14 (P15)
/Inputs/IN7SEN1: U8.3 (OUT2), U11.13 (P14)
/Inputs/IN8: J4.2, R26.2
/Inputs/IN8SEN0: U10.2 (OUT1), U11.16 (P17)
/Inputs/IN8SEN1: U10.3 (OUT2), U11.15 (P16)
/Inputs/IN9: J6.4, R34.2
/Inputs/IN9SEN0: U11.18 (P21), U14.2 (OUT1)
/Inputs/IN9SEN1: U11.17 (P20), U14.3 (OUT2)
/Inputs/IN10: J6.2, R44.2
/Inputs/IN10SEN0: U11.20 (P23), U16.2 (OUT1)
/Inputs/IN10SEN1: U11.19 (P22), U16.3 (OUT2)
/Inputs/IN11: J7.3, R52.2
/Inputs/IN11SEN0: U11.22 (P25), U18.2 (OUT1)
/Inputs/IN11SEN1: U11.21 (P24), U18.3 (OUT2)
/Inputs/IN12: J7.2, R60.2
/Inputs/IN12SEN0: U11.24 (P27), U20.2 (OUT1)
/Inputs/IN12SEN1: U11.23 (P26), U20.3 (OUT2)
A0: R13.2, U11.32 (~INT); also elsewhere on the board
A1: R41.1, SW2.2; also elsewhere on the board
D0: R40.1, SW1.2; also elsewhere on the board
GND: C25.1, C26.1, C27.1, C28.1, C29.1, C30.1, C31.1, C32.1, C33.1, C34.1, C35.1, C36.1, C37.1, C38.1, C39.1, C40.1, C41.1, C42.1, C43.1, C44.1, C45.1, C46.1, C47.1, C48.1, C49.1, C50.1, C51.1, C52.1, C53.1, D7.3 (GND), D8.3 (GND), D9.3 (GND), D10.3 (GND), D11.3 (GND), D12.3 (GND), J3.1, J4.1, J4.3, J5.1, J6.1, J6.3, J7.1, J8.1, J8.3, SW1.1, SW2.1, U7.5 (GND), U8.5 (GND), U9.5 (GND), U10.5 (GND), U11.25 (GND), U11.26 (ADDR), U11.33 (EP), U12.3 (GND), U13.5 (GND), U14.5 (GND), U15.5 (GND), U16.5 (GND), U17.5 (GND), U18.5 (GND), U19.5 (GND), U20.5 (GND); also elsewhere on the board
unnamed: C28.2, R14.1, R17.1, U7.4 (SENSE2)
unnamed: C29.2, R15.1, R19.1, U8.4 (SENSE2)
unnamed: C32.2, R22.1, R25.1, U9.4 (SENSE2)
unnamed: C33.2, R23.1, R27.1, U10.4 (SENSE2)
unnamed: C40.2, R30.1, R33.1, U13.4 (SENSE2)
unnamed: C41.2, R31.1, R35.1, U14.4 (SENSE2)
unnamed: C44.2, R38.1, R43.1, U15.4 (SENSE2)
unnamed: C45.2, R39.1, R45.1, U16.4 (SENSE2)
unnamed: C48.2, R48.1, R51.1, U17.4 (SENSE2)
unnamed: C49.2, R49.1, R53.1, U18.4 (SENSE2)
unnamed: C52.2, R56.1, R59.1, U19.4 (SENSE2)
unnamed: C53.2, R57.1, R61.1, U20.4 (SENSE2)
unnamed: D7.1 (IO1), R24.1, R25.2
unnamed: D7.2 (IO2), R16.1, R17.2
unnamed: D8.1 (IO1), R26.1, R27.2
unnamed: D8.2 (IO2), R18.1, R19.2
unnamed: D9.1 (IO1), R42.1, R43.2
unnamed: D9.2 (IO2), R32.1, R33.2
unnamed: D10.1 (IO1), R44.1, R45.2
unnamed: D10.2 (IO2), R34.1, R35.2
unnamed: D11.1 (IO1), R58.1, R59.2
unnamed: D11.2 (IO2), R50.1, R51.2
unnamed: D12.1 (IO1), R60.1, R61.2
unnamed: D12.2 (IO2), R52.1, R53.2
unnamed: F1.2, J3.4
unnamed: F2.2, J5.4
unnamed: R10.2, R15.2, U8.6 (SENSE1)
unnamed: R9.2, R14.2, U7.6 (SENSE1)
unnamed: R20.2, R22.2, U9.6 (SENSE1)
unnamed: R21.2, R23.2, U10.6 (SENSE1)
unnamed: R28.2, R30.2, U13.6 (SENSE1)
unnamed: R29.2, R31.2, U14.6 (SENSE1)
unnamed: R36.2, R38.2, U15.6 (SENSE1)
unnamed: R37.2, R39.2, U16.6 (SENSE1)
unnamed: R46.2, R48.2, U17.6 (SENSE1)
unnamed: R47.2, R49.2, U18.6 (SENSE1)
unnamed: R54.2, R56.2, U19.6 (SENSE1)
unnamed: R55.2, R57.2, U20.6 (SENSE1)
SCL: R12.2, TP4.1, U11.29 (SCL); also elsewhere on the board
SDA: R11.2, TP3.1, U11.30 (SDA); also elsewhere on the board
VSW1: J7.4; also elsewhere on the board

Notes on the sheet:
Radio
Address 010 0010
Photo Eye
Each input supports Normally Open, Normally Closed, and 10k Monitered connections.
+12V (01)
IN1 (02)
IN2 (03)
GND (04)
+12V (05)
IN3 (06)
GND (08)
GND (10)
GND (12)
IN4 (07)
IN5 (09)
IN6 (11)
GND (14)
IN7 (13)
GND (16)
IN8 (15)
GND (18)
IN9 (17)
GND (20)
IN10 (19)
+12V (21)
IN11 (22)
IN12 (23)
GND (24)
Input
Input Reference
All IC’s
Description
10k Monitored Input
Normally Open Input
Current
40uA
0uA
49uA
Idle Currents
Normally Closed Input

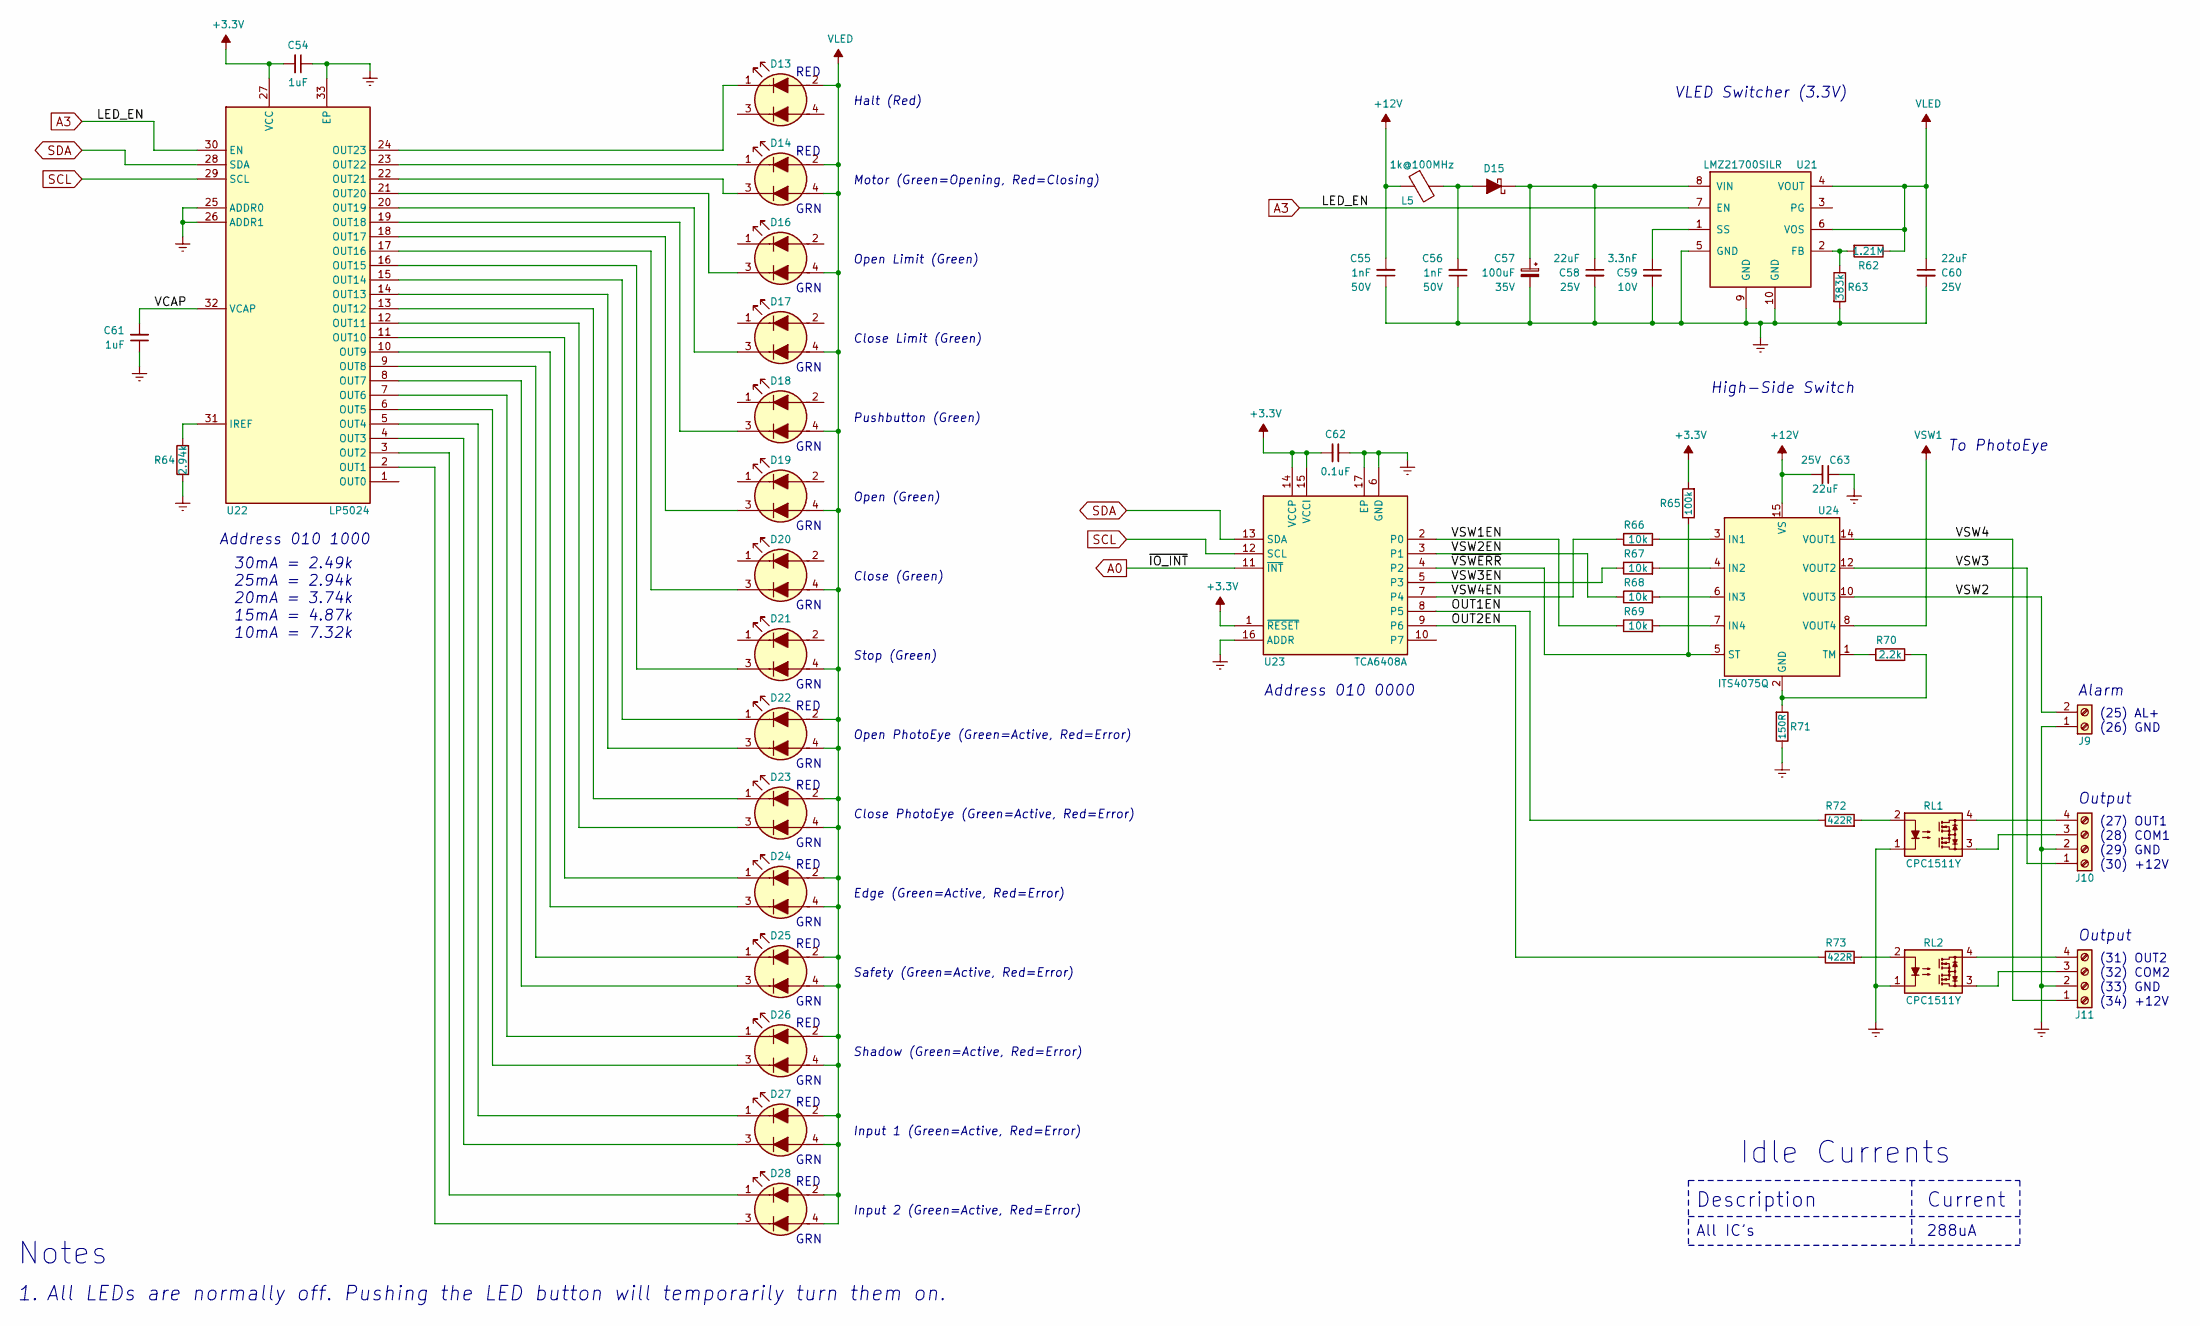
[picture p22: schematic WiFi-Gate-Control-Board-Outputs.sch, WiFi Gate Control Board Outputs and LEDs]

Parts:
C54, C61: 1uF; C_0603_1608Metric; Voltage 50V; Tolerance 10%; Part Number UMK107BJ105KA-T
C55, C56: 1nF; C_0603_1608Metric; Voltage 50V; Tolerance 10%; Part Number VJ0603Y102KXAAC31
C57: 100uF; CP_Elec_8x10; Voltage 35V; Tolerance 20%; Part Number EMVH350ADA101MHA0G
C58, C60, C63: 22uF; C_0805_2012Metric; Voltage 25V; Tolerance 20%; Part Number TMK212BBJ226MG-TT
C59: 3.3nF; C_0603_1608Metric; Voltage 10V; Tolerance 5%; Part Number VJ0603Y332JXQPW1BC
C62: 0.1uF; C_0603_1608Metric; Voltage 50V; Tolerance 5%; Part Number CC603JRX7R9BB104
D13, D14, D16, D17, D18, D19, D20, D21, D22, D23, D24, D25, D26, D27, D28: Red/Green; LED_Avago_PLCC4_3.2x2.8mm_CW; Part Number HSMF-A203-A00J1
D15: DFLS130; D_PowerDI-123; Part Number DFLS130LQ
J9: Screw Header 2 Pos; PhoenixContact_MSTBVA_2,5_2-G-5,08_1x02_P5.08mm_Vertical; Part Number 1755736
J10, J11: Screw Header 4 Pos; PhoenixContact_MSTBVA_2,5_4-G-5,08_1x04_P5.08mm_Vertical; Part Number 1755752
L5: 1k@100MHz; L_1206_3216Metric; Part Number BLM31KN102SH1L
R62: 1.21M; R_0603_1608Metric; Tolerance 1%; Part Number RC0603FR-071M21L
R63: 383k; R_0603_1608Metric; Tolerance 1%; Part Number ERJ-3EKF3833V
R64: 2.94k; R_0603_1608Metric; Tolerance 1%; Part Number ERJ-3EKF2941V
R65: 100k; R_0603_1608Metric; Tolerance 1%; Part Number ERJ-3EKF1003V
R66, R67, R68, R69: 10k; R_0603_1608Metric; Tolerance 0.5%; Part Number RR0816P-103-D
R70: 2.2k; R_0603_1608Metric; Tolerance 1%; Part Number ERJ-3EKF2201V
R71: 150R; R_1218_3246Metric; Tolerance 1%; Part Number CRCW1218150RFKEK
R72, R73: 422R; R_0603_1608Metric; Tolerance 1%; Part Number ERJ-3EKF4220V
RL1, RL2: CPC1511Y; Relay_IXYS_PowerSIP; Part Number CPC1511Y
U21: LMZ21700; Converter_DCDC_Texas-SIL0008E; Part Number LMZ21700SILR
U22: LP5024; QFN-32-1EP_4x4mm_P0.4mm_EP2.9x2.9mm_ThermalVias; Part Number LP5024RSMR
U23: TCA6408A; VQFN-16-1EP_3x3mm_P0.5mm_EP1.45x1.45mm_ThermalVias; Part Number TCA6408ARGTR
U24: ITS4075Q; Infineon_PG-TSDSO-14-22; Part Number ITS4075Q-EP-DXUMA1

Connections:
+3.3V: C54.2, C62.2, R65.2, U22.27 (VCC), U23.1 (~RESET), U23.14 (VCCP), U23.15 (VCCI); also elsewhere on the board
+12V: C55.2, C63.2, L5.1, U24.15 (VS); also elsewhere on the board
/Outputs and LEDs/OUT1EN: R72.1, U23.8 (P5)
/Outputs and LEDs/OUT2EN: R73.1, U23.9 (P6)
/Outputs and LEDs/VCAP: C61.2, U22.32 (VCAP)
/Outputs and LEDs/VSW1EN: R69.1, U23.2 (P0)
/Outputs and LEDs/VSW2: J9.2, U24.10 (VOUT3)
/Outputs and LEDs/VSW2EN: R68.1, U23.3 (P1)
/Outputs and LEDs/VSW3: J10.1, U24.12 (VOUT2)
/Outputs and LEDs/VSW3EN: R67.1, U23.5 (P3)
/Outputs and LEDs/VSW4: J11.1, U24.14 (VOUT1)
/Outputs and LEDs/VSW4EN: R66.1, U23.7 (P4)
/Outputs and LEDs/~VSWERR: R65.1, U23.4 (P2), U24.5 (ST)
A0: U23.11 (~INT); also elsewhere on the board
A3: U21.7 (EN), U22.30 (EN); also elsewhere on the board
GND: C54.1, C55.1, C56.1, C57.2, C58.2, C59.2, C60.2, C61.1, C62.1, C63.1, J9.1, J10.2, J11.2, R63.2, R64.1, R71.1, RL1.1, RL2.1, U21.5 (GND), U21.9 (GND), U21.10 (GND), U22.25 (ADDR0), U22.26 (ADDR1), U22.33 (EP), U23.6 (GND), U23.16 (ADDR), U23.17 (EP); also elsewhere on the board
unnamed: C56.2, D15.2 (A), L5.2
unnamed: C57.1, C58.1, D15.1 (K), U21.8 (VIN)
unnamed: C59.1, U21.1 (SS)
unnamed: D13.1 (K1), U22.24 (OUT23)
unnamed: D14.1 (K1), U22.23 (OUT22)
unnamed: D14.3 (K2), U22.22 (OUT21)
unnamed: D16.3 (K2), U22.21 (OUT20)
unnamed: D17.3 (K2), U22.20 (OUT19)
unnamed: D18.3 (K2), U22.19 (OUT18)
unnamed: D19.3 (K2), U22.18 (OUT17)
unnamed: D20.3 (K2), U22.17 (OUT16)
unnamed: D21.3 (K2), U22.16 (OUT15)
unnamed: D22.1 (K1), U22.15 (OUT14)
unnamed: D22.3 (K2), U22.14 (OUT13)
unnamed: D23.1 (K1), U22.13 (OUT12)
unnamed: D23.3 (K2), U22.12 (OUT11)
unnamed: D24.1 (K1), U22.11 (OUT10)
unnamed: D24.3 (K2), U22.10 (OUT9)
unnamed: D25.1 (K1), U22.9 (OUT8)
unnamed: D25.3 (K2), U22.8 (OUT7)
unnamed: D26.1 (K1), U22.7 (OUT6)
unnamed: D26.3 (K2), U22.6 (OUT5)
unnamed: D27.1 (K1), U22.5 (OUT4)
unnamed: D27.3 (K2), U22.4 (OUT3)
unnamed: D28.1 (K1), U22.3 (OUT2)
unnamed: D28.3 (K2), U22.2 (OUT1)
unnamed: J10.3, RL1.3
unnamed: J10.4, RL1.4
unnamed: J11.3, RL2.3
unnamed: J11.4, RL2.4
unnamed: R62.2, R63.1, U21.2 (FB)
unnamed: R64.2, U22.31 (IREF)
unnamed: R66.2, U24.3 (IN1)
unnamed: R67.2, U24.4 (IN2)
unnamed: R68.2, U24.6 (IN3)
unnamed: R69.2, U24.7 (IN4)
unnamed: R70.1, U24.1 (TM)
unnamed: R70.2, R71.2, U24.2 (GND)
unnamed: R72.2, RL1.2
unnamed: R73.2, RL2.2
SCL: U22.29 (SCL), U23.12 (SCL); also elsewhere on the board
SDA: U22.28 (SDA), U23.13 (SDA); also elsewhere on the board
VLED: C60.1, D13.2 (A1), D14.2 (A1), D14.4 (A2), D16.4 (A2), D17.4 (A2), D18.4 (A2), D19.4 (A2), D20.4 (A2), D21.4 (A2), D22.2 (A1), D22.4 (A2), D23.2 (A1), D23.4 (A2), D24.2 (A1), D24.4 (A2), D25.2 (A1), D25.4 (A2), D26.2 (A1), D26.4 (A2), D27.2 (A1), D27.4 (A2), D28.2 (A1), D28.4 (A2), R62.1, U21.4 (VOUT), U21.6 (VOS); also elsewhere on the board
VSW1: U24.8 (VOUT4); also elsewhere on the board

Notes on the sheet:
Output
(27) OUT1
(28) COM1
(29) GND
(30) +12V
(26) GND
(25) AL+
Alarm
(32) COM2
(34) +12V
(33) GND
(31) OUT2
To PhotoEye
GRN
RED
Motor (Green=Opening, Red=Closing)
Open Limit (Green)
VLED Switcher (3.3V)
Address 010 1000
Address 010 0000
High-Side Switch
Shadow (Green=Active, Red=Error)
Safety (Green=Active, Red=Error)
Edge (Green=Active, Red=Error)
Close Limit (Green)
Close PhotoEye (Green=Active, Red=Error)
Open PhotoEye (Green=Active, Red=Error)
Stop (Green)
Close (Green)
Open (Green)
Pushbutton (Green)
Halt (Red)
Input 1 (Green=Active, Red=Error)
Input 2 (Green=Active, Red=Error)
30mA = 2.49k 25mA = 2.94k 20mA = 3.74k 15mA = 4.87k 10mA = 7.32k
All IC’s
Description
Current
288uA
Idle Currents

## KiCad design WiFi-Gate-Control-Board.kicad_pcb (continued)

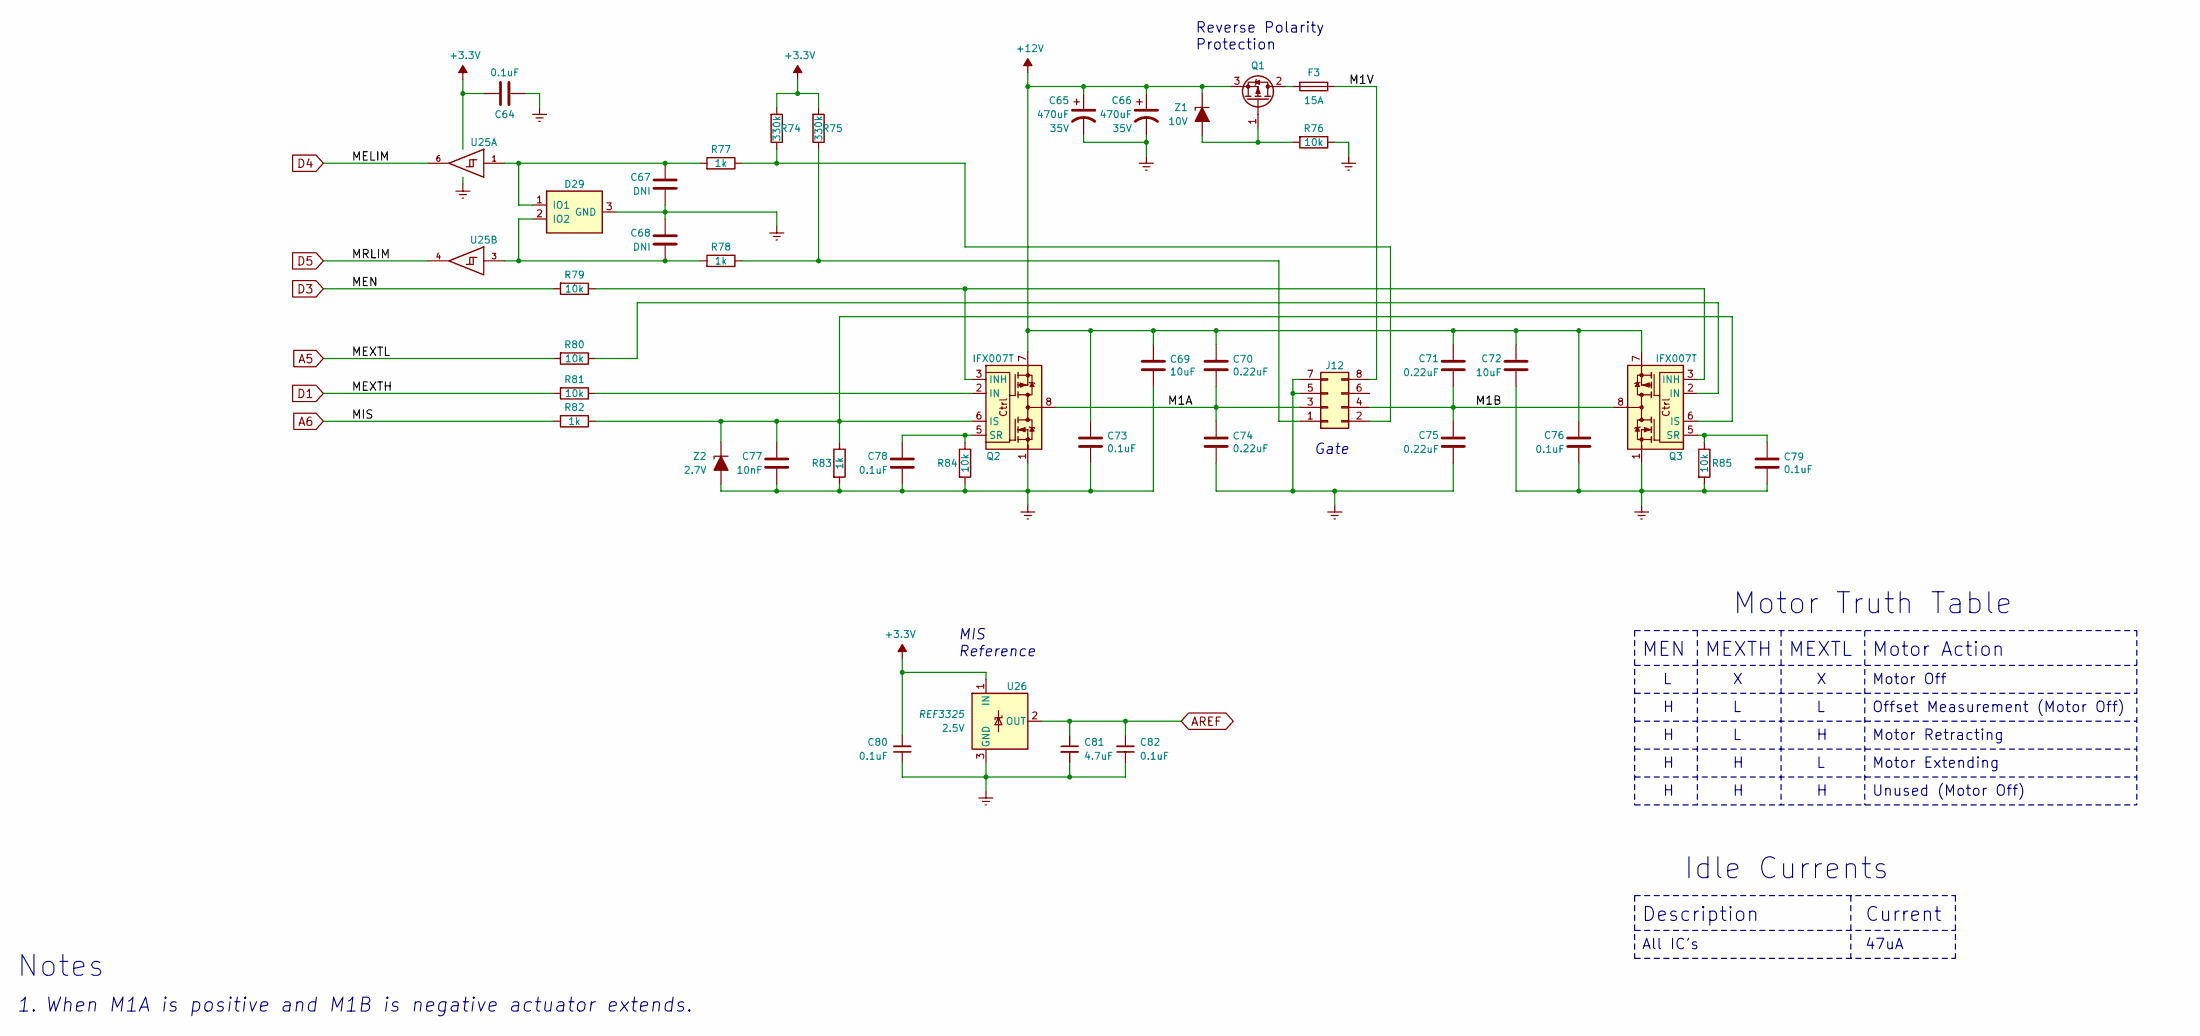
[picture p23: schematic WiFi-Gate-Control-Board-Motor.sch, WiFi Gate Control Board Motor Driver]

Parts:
C64, C73, C76, C78, C79, C80, C82: 0.1uF; C_0603_1608Metric; Voltage 50V; Tolerance 5%; Part Number CC603JRX7R9BB104
C65, C66: 470uF; CP_Radial_D16.0mm_P7.50mm; Voltage 35V; Tolerance 20%; Part Number UPM1V471MHD6
C67, C68: DNI; C_0603_1608Metric
C69, C72: 10uF; C_1206_3216Metric; Voltage 50V; Tolerance 10%; Part Number CGA5L1X7R1H106K160AC
C70, C71, C74, C75: 0.22uF; C_0603_1608Metric; Voltage 50V; Tolerance 10%; Part Number UMK107B7224KA-TR
C77: 10nF; C_0603_1608Metric; Voltage 50V; Tolerance 5%; Part Number VJ0603Y103JXACW1BC
C81: 4.7uF; C_0603_1608Metric; Voltage 6.3V; Tolerance 10%; Part Number JMK107BB7475KA-T
D29: TPD2E2U06; SOT-323_SC-70; Part Number TPD2E2U06QDCKRQ1
F3: 15A; Fuseholder_Blade_Mini_Keystone_3568; Part Number 3568
J12: Motor; TE_MATE-N-LOK_350212-1_2X04_P4.95_Vertical; Part Number 350212-1
Q1: IPD90P03P4L-04; TO-252-2; Part Number IPD90P03P4L-04
Q2, Q3: IFX007T; TO-263-7_TabPin8; Part Number IFX007TAUMA1
R74, R75: 330k; R_1206_3216Metric; Tolerance 5%; Part Number ERJ-P08J334V
R76, R79, R80, R81, R84, R85: 10k; R_0603_1608Metric; Tolerance 0.5%; Part Number RR0816P-103-D
R77, R78: 1k; R_1206_3216Metric; Tolerance 0.5%; Part Number AC1206DR-071KL
R82, R83: 1k; R_0603_1608Metric; Tolerance 1%; Part Number ERJ-3EKF1001V
U25: 74LVC2G17; SOT-23-6; Part Number SN74LVC2G17DBVR
U26: REF3325; SOT-23; Voltage 2.5V; Part Number REF3325AIDBZR
Z1: 10V; D_SOT-23_ANK; Part Number SZBZX84C10LT1G
Z2: 2.7V; D_SOT-23_ANK; Part Number SZBZX84C2V7LT1G

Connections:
+3.3V: C64.2, C80.2, R74.2, R75.2, U25.5 (VCC), U26.1 (IN); also elsewhere on the board
+12V: C65.1, C66.1, C69.1, C70.1, C71.1, C72.1, C73.1, C76.1, Q1.3 (S), Q2.7, Q3.7, Z1.1 (K); also elsewhere on the board
/Motor Driver/M1A: C70.2, C74.1, J12.3, Q2.4, Q2.8
/Motor Driver/M1B: C71.2, C75.1, J12.4, Q3.4, Q3.8
/Motor Driver/M1V: F3.1, J12.8
A5: R80.2; also elsewhere on the board
A6: R82.2; also elsewhere on the board
AREF: C81.1, C82.2, U26.2 (OUT); also elsewhere on the board
D1: R81.2; also elsewhere on the board
D3: R79.2; also elsewhere on the board
D4: U25.6; also elsewhere on the board
D5: U25.4; also elsewhere on the board
GND: C64.1, C65.2, C66.2, C67.2, C68.1, C69.2, C72.2, C73.2, C74.2, C75.2, C76.2, C77.2, C78.2, C79.2, C80.1, C81.2, C82.1, D29.3 (GND), J12.5, J12.7, Q2.1, Q3.1, R76.1, R83.2, R84.2, R85.2, U25.2 (GND), U26.3 (GND), Z2.2 (A); also elsewhere on the board
unnamed: C67.1, D29.1 (IO1), R77.2, U25.1
unnamed: C68.2, D29.2 (IO2), R78.2, U25.3
unnamed: C77.1, Q2.6 (IS), Q3.6 (IS), R82.1, R83.1, Z2.1 (K)
unnamed: C78.1, Q2.5 (SR), R84.1
unnamed: C79.1, Q3.5 (SR), R85.1
unnamed: F3.2, Q1.2 (D)
unnamed: J12.1, R75.1, R78.1
unnamed: J12.2, R74.1, R77.1
unnamed: Q1.1 (G), R76.2, Z1.2 (A)
unnamed: Q2.2 (IN), R81.1
unnamed: Q2.3 (INH), Q3.3 (INH), R79.1
unnamed: Q3.2 (IN), R80.1

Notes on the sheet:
Gate
When M1A is positive and M1B is negative actuator extends.
Reverse Polarity Protection
MEXTH
MEN
Motor Action
Motor Off
Motor Extending
Motor Retracting
MIS Reference
All IC’s
Description
Current
47uA
Idle Currents
Notes
MEXTL
Offset Measurement (Motor Off)
Unused (Motor Off)
Motor Truth Table

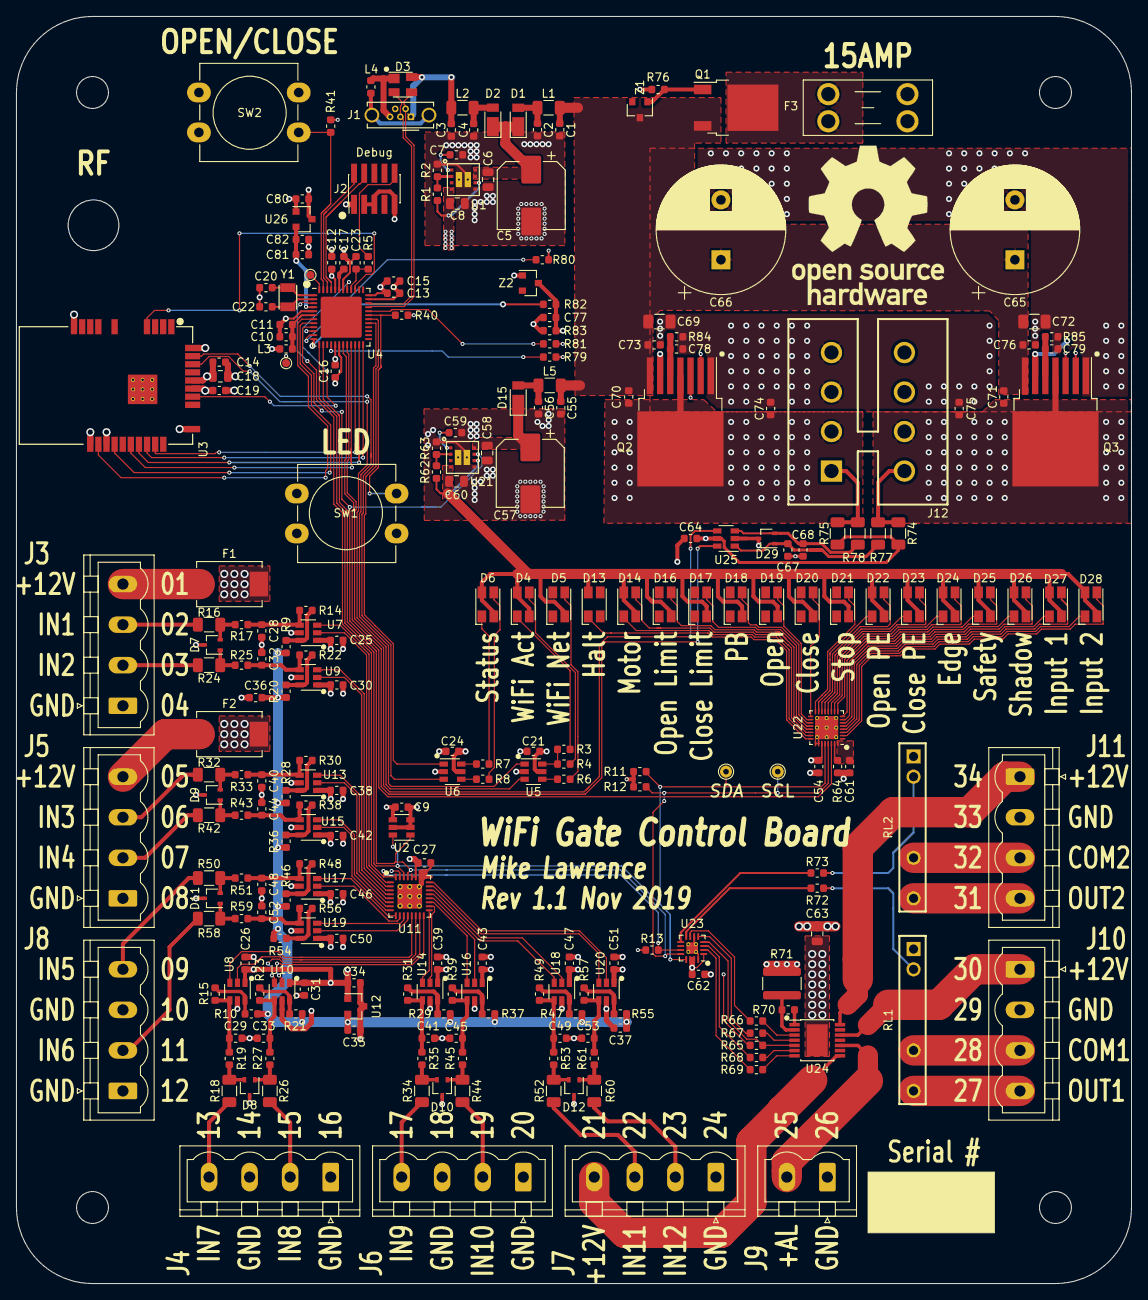
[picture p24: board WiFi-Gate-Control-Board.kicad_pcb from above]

Board: 4 copper layers, 139.7 x 158.8 mm, 257 parts (0 on the bottom side), 200 nets.

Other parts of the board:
RF: Val**; SMA_Bulkhead_Mount

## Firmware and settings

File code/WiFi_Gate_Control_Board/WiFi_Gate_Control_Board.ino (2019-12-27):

/*
  WiFi Gate Control Board 
  
  This code is designed to replace the functionality of US Automatic gate control board
  while adding WiFi access and Home Assistant control via MQTT.
  The board is compatible with an Arduino MKR1000.
  
  Built with Arduino IDE 1.8.10
  
  The following libraries must be installed using Library Manager:
  
    WiFi101 version 0.16.0 by Arduino
      WINC1501 Model B firmware version 19.6.1
    WiFi101OTA version 1.0.2 by Arduino
    SD version 1.2.4 by Arduino
    FreeRTOS_SAMD21 version 1.0.0 by BriscoeTech
    MQTT version 2.4.5 by Joel Gaehwiler
    I2C_DMAC version 1.1.8 by Martin Lindupp

  Clock configuration
    XOSC32k is enabled, Arduino startup.c
    DFLL48M is enabled, Arduino startup.c
    OSC8M is disable, WiFiGate_Control_Board.c, changed from Arduino startup.c, ADC clock
  
  Generic Clock configuration
    GCLK0, Src DFLL48M, 48MHz Out, Arduino startup.c, Main clock
    GCLK1, Src XOSC32K, 32.768kHz Out, Arduino startup.c, ref clock to DFLL48M, ref clock to GCLK4
    GCLK2, Src OSCULP32K, 1.024kHz Out, WDTZero.ino, Watchdog Timer (WDT) clock 
    GCLK3, Src DFLL48M, 8MHz Out, hal.ino, changed from Arduino startup.c, ADC clock
    GCLK4, Src XOSC32K, 1.024kHz Out, RTCZero.cpp, RTC clock

  Status LED Flashing Amber or Red indicates a hard fault
    1 flash   - RTOS stack overflow
    2 flashes - RTOS malloc failed
    3 flashes - RTOS fatal error
    4 flashes - I2C hardware not detected
    5 flashes - WINC1500 module not detected

  Copyright (c) 2019 Mike Lawrence
  
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
  THE SOFTWARE IS PROVIDED "AS IS", WITHOUT WARRANTY OF ANY KIND, EXPRESS OR
  IMPLIED, INCLUDING BUT NOT LIMITED TO THE WARRANTIES OF MERCHANTABILITY,
  FITNESS FOR A PARTICULAR PURPOSE AND NONINFRINGEMENT. IN NO EVENT SHALL THE
  AUTHORS OR COPYRIGHT HOLDERS BE LIABLE FOR ANY CLAIM, DAMAGES OR OTHER
  LIABILITY, WHETHER IN AN ACTION OF CONTRACT, TORT OR OTHERWISE, ARISING FROM,
  OUT OF OR IN CONNECTION WITH THE SOFTWARE OR THE USE OR OTHER DEALINGS IN THE
  SOFTWARE.
*/
// Modify ../WiFi101/src/bsp/include/nm_bsp_internal.h library file
// so that CONF_PERIPH is defined. This will enabled LEDS from WiFi Module
#include "state.h"
#include "network.h"
#include "WiFi_Gate_Control_Board.h"
#include <MemoryFree.h>

/******************************************************************
 * Definitions in arduino_secrets.h
 ******************************************************************/
/*
#define SECRET_SSID             "SSID of your WiFi network"
#define SECRET_PASSWORD         "Password for your WIFi network"
// IP address of MQTT server, host name may work but I've never tried
#define MQTT_SERVER             "192.168.0.230"
#define MQTT_SERVERPORT         1883
// MQTT user name and password leave as empty string if not used
#define MQTT_USERNAME           ""
#define MQTT_PASSWORD           ""
// Over-The-Air Update password if used
#define OTA_PASSWORD            "password"
*/

/******************************************************************
 * Global Variables
 ******************************************************************/
// FreeRTOS task handles
TaskHandle_t h_HALTask;
TaskHandle_t h_NETTask;
TaskHandle_t h_STATETask;
TaskHandle_t h_MOTORTask;

/******************************************************************
 * Standard Arduino setup function
 ******************************************************************/
void setup() {
  // Serial setup
  #ifdef ENABLE_SERIAL
  Serial.begin(115200);
  //delay(2000);
  vNopDelayMS(2000);
  #endif
  
  // Announce who we are and software version
  Println("\nWiFi Gate Control Board: " BOARD_NAME);
  Println("  Software Version: " VERSION);
  Println("Initializing HAL");

  // Initialize HAL
  if (!HAL.begin()) {
    Println("Failed to initialize hardware devices. Nothing can be done. Halt!");
    ERR.setHaltError(ERROR_HAL_HALT);                 // This function will flash LED error and never return 
  }

  // WiFi setup
  if (WiFi.status() == WL_NO_SHIELD) {                // check for the presence of the WINC1500
    Println("Failed to find WINC1500 WiFi Module. Nothing can be done. Halt!");
    ERR.setHaltError(ERROR_WIFI_HALT);                // This function will flash error LED and never return 
  }
  Println("Found WINC1500 WiFi Module");
  #ifdef ENABLE_SERIAL
  // Display Firmware Version
  Print("  Firmware Version: ");
  Println(WiFi.firmwareVersion());
  Print("  Library Version: ");
  Println(WIFI_FIRMWARE_LATEST_MODEL_B);
  #endif

  // arduino startup configures OSC8M, source to GCLK3, output 8MHz
  // not sure why, motor.ino changes GCLK3 source to DFLL48M, output 8MHz
  // disable OSC8M because it is no longer used
  SYSCTRL->OSC8M.bit.ENABLE = 1;

  // Watchdog initialize
  if (WDTZero.begin()) {
    Println("Watchdog enabled");
  } else {
    Println("Watchdog NOT enabled");
  }

  Println("");
  
  // FreeRTOS error LED connections
  vSetErrorLed(STATUS_RED_LED, HIGH);

  // create tasks
  xTaskCreate(thread_hal, "HAL Task", 256, NULL, tskIDLE_PRIORITY + 2, &h_HALTask);
  xTaskCreate(thread_motor, "MOTOR Task", 256, NULL, tskIDLE_PRIORITY + 4, &h_MOTORTask);
  #ifndef ENABLE_CALIBRATION_MODE
  xTaskCreate(thread_state, "STATE Task", 256, NULL, tskIDLE_PRIORITY + 3, &h_STATETask);
  xTaskCreate(thread_net, "NET Task", 512, NULL, tskIDLE_PRIORITY + 1, &h_NETTask);
  #endif

  Log("Heap Remaining: ");
  Print( freeMemory() );
  Println(" bytes");

  // start the RTOS, this function will never return and will schedule the tasks.
  vTaskStartScheduler();
}

/******************************************************************
 * FreeRTOS idle loop
 * Should never be called because the Network Task has a 
 * higher priority and should never yield to this task.
 ******************************************************************/
void loop() {
//  yield();
//  static uint32_t lastTempPublish = 0 - (TEMP_RATE + 10);
//  static uint8_t lastPushbuttonState = false;
//  static uint8_t calSampleInProgress = false;
//      
//  // Reset the watchdog every time loop() is called
//  WDTZero.reset();
//  
////  if (calSampleInProgress) {
////    // we are waiting for a calibration sample to finish
////    if (!MOTOR.calSampleBusy()) {
////      // calibration sample is done
////      //MOTOR.motorOff();
////      Print("Motor calibration sample average = "); Println(MOTOR.calSampleGet());
////      calSampleInProgress = false;
////    }
////  } else {
//    // there is no calibration sample in progress
//    if (HAL.inputRead(IN_PUSHBUTTON)) {
//      // pushbutton was pressed, start a new calibration sample
//      calSampleInProgress = true;
//      Println("Starting Motor calibration sample average...");
////      MOTOR.motorOn(MOTOR_DIR_EXTEND);
//      delay(100);
////      digitalWrite(PIN_MOTOR_EXT_H, LOW);       // Set Half-bridges both low 
////      digitalWrite(PIN_MOTOR_EXT_L, LOW);
////      digitalWrite(PIN_MOTOR_EN, HIGH);         // Half-Bridges enabled
//      for (int i = 0; i < 600; i++) {
////        MOTOR.calSampleStart();
////        while (MOTOR.calSampleBusy()) {
//          delay(1000);
//          Print("Seconds="); Println(i+1);
////        }
////        Print("Motor calibration sample average = "); Println(MOTOR.calSampleGet());
//      }
//      MOTOR.motorOff();
////    }
//  }
//  // update last pushbutton state
//  lastPushbuttonState = HAL.inputRead(IN_PUSHBUTTON);
//  
//  // time to publish temperature?
//  if (xTaskGetTickCount() > lastTempPublish + TEMP_RATE) {
//    Print("Free RAM = "); Println(freeMemory());
//    lastTempPublish = xTaskGetTickCount();   // we just published
//  }
//
//
//  // We are using Scheduler library so we should yield or delay
//  delay(10);
}

/******************************************************************
 * HAL module motor thread function
 ******************************************************************/
static void thread_motor(void *pvParameters) {
  // Initialization of MOTOR is done in setup
  //Logln("MOTOR Task now running");
  
  // Loop forever
  while (true) {
    // run HAL Motor loop frequently
    HAL.motorLoop();
    // delay a bit before running the motor loop again
    delayMs(10);
  }
}

/******************************************************************
 * State module thread function
 ******************************************************************/
static void thread_state(void *pvParameters) {
  // Initialize State Machine
  //Logln("State Task now running");
  STATE.begin();

  // Loop forever
  while (true) {
    STATE.loop();
  }
}

/******************************************************************
 * HAL module thread function
 ******************************************************************/
static void thread_hal(void *pvParameters) {
  TickType_t previousWakeTick = xTaskGetTickCount();

  // Initialization of HAL is done in setup
  //Logln("HAL Task now running");
  
  // Loop forever
  while (true) {
    // run HAL loop frequently
    HAL.loop();
    // we want to run every so often
    delayMsUntil(&previousWakeTick, 2);
  }
}

/******************************************************************
 * Network module thread function (lowest priority task)
 ******************************************************************/
static void thread_net(void *pvParameters) {
  TickType_t freememUpdateTick = xTaskGetTickCount();

  // Initialize network
  //Logln("Network Task now running");
  NET.begin();

  // Loop forever
  while (true) {
    NET.loop();

    // display free memory info
    if (xTaskGetTickCount() - freememUpdateTick > 60000) {
      freememUpdateTick += 60000;
      Log("Thread free bytes (NET: ");
      Print(uxTaskGetStackHighWaterMark( h_NETTask ));
      Print(", HAL: ");
      Print(uxTaskGetStackHighWaterMark( h_HALTask ));
      Print(", STATE: ");
      Print(uxTaskGetStackHighWaterMark( h_STATETask ));
      Print(", MOTOR: ");
      Print(uxTaskGetStackHighWaterMark( h_MOTORTask ));
      Println(")");
    }
  }
}

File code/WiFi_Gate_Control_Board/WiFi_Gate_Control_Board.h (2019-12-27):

/*
  WiFi Gate Control Board Project wide defines

  Copyright (c) 2019 Mike Lawrence

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
  THE SOFTWARE IS PROVIDED "AS IS", WITHOUT WARRANTY OF ANY KIND, EXPRESS OR
  IMPLIED, INCLUDING BUT NOT LIMITED TO THE WARRANTIES OF MERCHANTABILITY,
  FITNESS FOR A PARTICULAR PURPOSE AND NONINFRINGEMENT. IN NO EVENT SHALL THE
  AUTHORS OR COPYRIGHT HOLDERS BE LIABLE FOR ANY CLAIM, DAMAGES OR OTHER
  LIABILITY, WHETHER IN AN ACTION OF CONTRACT, TORT OR OTHERWISE, ARISING FROM,
  OUT OF OR IN CONNECTION WITH THE SOFTWARE OR THE USE OR OTHER DEALINGS IN THE
  SOFTWARE.
*/

#ifndef WIFI_GATE_CONTROL_BOARD_H
#define WIFI_GATE_CONTROL_BOARD_H

#include <WiFi101.h>
#include <FreeRTOS_SAMD21.h>
#include "WiFiRTC.h"
#include "WDTZero.h"
#include "error.h"
#include "hal.h"
#include "arduino_secrets.h"

/******************************************************************
 * Build defines
 ******************************************************************/
// Enable Watchdog Timer
#define ENABLE_WATCHDOG
// Enable OTA updates
#define ENABLE_OTA_UPDATES
// Enable Serial on USB
#define ENABLE_SERIAL
// Enable Low Power Mode on WiFi
#define ENABLE_WIFI_LOW_POWER
// enable calibration mode
//#define ENABLE_CALIBRATION_MODE
// Current Version
#define VERSION                   "1.0"

/******************************************************************
 * Enumerations
 ******************************************************************/
// The two types of Gate directions
enum Gate_Dir_Enum {GATE_PULL_TO_OPEN = 0, GATE_PUSH_TO_OPEN};

/******************************************************************
 * Application defines
 ******************************************************************/
// Name of this board, each board should be unique
// Used as MQTT Client ID, HASS Name, and OTA Name
#define BOARD_NAME                "New Front Gate"
// NTP server used to update local time, can be IP Address or name
#define NTP_SERVER                "pool.ntp.org"
// timezone difference from GMT in hours (Standard Time difference)
#define TZDIFF                    -6
// input debounce time in milliseconds
#define DEBOUNCE_TIME             100
// temperature measurement time in milliseconds, Must be greater than 5 seconds
#define TEMP_RATE                 (1*60*1000)
// Length of time in milliseconds LEDS stay on after pushbutton input
#define LED_ON_TIME               (5*60*1000) 

/******************************************************************
 * Gate Defines
 *   Here is where you change the basic gate settings
 ******************************************************************/
// this defines which way the linear actuator has to move to open
//   GATE_PULL_TO_OPEN or GATE_PUSH_TO_OPEN
#define GATE_DIRECTION            GATE_PULL_TO_OPEN
// how long (ms) gate remains open before automatically closing
// range 0 - 90 seconds or 0 - 90,000 milliseconds, default 60,000
// set to 0 to turn off automatic close
#define GATE_AUTO_CLOSE           60 * 1000
// how long (ms) gate is allowed to run without reaching limits.
// range 5 - 120 seconds or 5,000 - 120,000 milliseconds, default 60,000
#define GATE_RUN_TIME             60 * 1000
// how long (ms) lamp is active prior to gate movement
// default 0, range 0 - 5 seconds or 0 - 5,000 milliseconds
#define GATE_LAMP_DELAY           0
// how long (ms) magnetic lock is activated to release lock prior to gate moving
// default 1000, range 0 - 5 seconds or 0 - 5,000 milliseconds
#define GATE_LOCK_DELAY           1 * 1000
// this defines the how long (ms) in over-current before tripping
// range 0 - 5 seconds of 0 - 5,000 milliseconds
#define GATE_OC_TRIP_TIME         500
// this defines the over-current level to trip in time GATE_OC_TRIP_TIME
// value is in 10mA steps (i.e. 20 amp = 20 * 100 = 2000)
#define GATE_OC_TRIP_CURRENT      5 * 100
// this defines the peak over-current to trip instantly
// value is in 10mA steps (i.e. 20 amp = 20 * 100 = 2000)
#define GATE_OC_TRIP_PEAK         20 * 100

/******************************************************************
 * Gate Input Type Defines
 *   Here is where you change the board inputs to specific types
 *   Look in hal.h for IN_Type_Enum for valid input types
 ******************************************************************/
#define BOARD_IN1                 IN_TYPE_PUSHBUTTON_NO
#define BOARD_IN2                 IN_TYPE_NONE
#define BOARD_IN3                 IN_TYPE_NONE
#define BOARD_IN4                 IN_TYPE_NONE
#define BOARD_IN5                 IN_TYPE_PUSHBUTTON_NO
#define BOARD_IN6                 IN_TYPE_OPEN_NO
#define BOARD_IN7                 IN_TYPE_NONE
#define BOARD_IN8                 IN_TYPE_NONE
#define BOARD_IN9                 IN_TYPE_NONE
#define BOARD_IN10                IN_TYPE_NONE
#define BOARD_IN11                IN_TYPE_OPEN_PHOTOEYE_10K
#define BOARD_IN12                IN_TYPE_NONE
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

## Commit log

2019-10-20 Initial commit.
    Design still in progress.
    [WiFi-Gate-Control-Board-B_Cu.gbl, WiFi-Gate-Control-Board-B_Mask.gbs, WiFi-Gate-Control-Board-B_SilkS.gbo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]
2019-10-24 Rev 1.0 Release
    Added input design and calculations. Added BOM. Added Fuse 3D Model.
    [WiFi-Gate-Control-Board-BOM.csv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]
2019-12-05 PCB to Rev 1.1
    Fixed missing Reference Designators on top Silkscreen.
    Reset input on TCA6424A and TCA6408A now connected to 3.3V.
    Added series Schottky Diode to LED power supply input.
    Replaced 1000uF main power capacitor with two 470uF capacitors.
    Replaced DS18B20 temperature sensor with TMP100 temperature sensor.
    Increased LED currents to 25mA
    Removed U26 inverter and connected U3 IN pin directly to processor. Now able to measure unloaded offset current.
    [WiFi-Gate-Control-Board-BOM-Gen.csv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]
2019-12-08 Changed Cortex Debug connector. Added fabrication pdf.
    [WiFi-Gate-Control-Board-BOM-Gen.csv, WiFi-Gate-Control-Board-BOM.csv, WiFi-Gate-Control-Board.kicad_pcb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]
2019-12-08 Remove old fabriction pdf. Update board image.
2019-12-27 Added Calibration Mode.
2021-11-08 Update README.md
    https://github.com/mikelawrence/WiFi-Gate-Control-Board
